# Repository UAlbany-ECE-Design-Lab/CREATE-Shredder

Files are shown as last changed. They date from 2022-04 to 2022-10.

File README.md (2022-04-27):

# CREATE-Shredder Extraction System 2021-2022 ReadMe

This ReadMe file uses Markdown formating.  Helpful cheat sheet is available here: 	[Markdown Cheat Sheet](https://www.markdownguide.org/cheat-sheet/)

## Team Members
Joseph Salgado - 
Michael George - 
Guillermo Esteban Mijancos
Team

## Hardware Dependencies
This project is very hardware oriented, and once we describe each item it will show how intuitive the hole system is.

1. We use a D/D Blower w/ Motor, 208-230/460 V. For our desired system we need a reliable and robust blower/motor
combination. This blower has an 11-inch turbine which is large enough to not get jammed or
clogged by small paper shreds. The motor that comes with this setup is a 1 horsepower 3
phase electric motor that can spin upwards of 3500 RPM. With our system, we plan on using
4 inches ducting for the inlet and the exhaust side and with a 4-inch outlet, this blower can
push nearly 560 CFM which should be plenty for our application
Motor

2. We use a 3 Phase 30A 3.7KW Maintained Self Lock On/Off Power Pushbutton Switch. It has ideal specifications to deal with the power needed by the motor and has the perfect 
functionality we are looking for our system. Once pressed On it maintains like that until we press the Off button.
Switch

3.We use a MODEL GN3442 GAYLORD COVER because the goal of the system designed in this project is to get the shredded paper
automatically into the big brown box provided by the mailing service company. In order to do
that, we require this component because the whole system works around a motor/blower
that creates wind gusts that would make kind of sloppy the whole movement of the paper.
This device provides a specific and convenient solution, covering the box and just letting the
tube with the shredded paper have access to it. This way, we use the cover until the box is
full and then easily remove it to get the shredded paper out.

gaylordCover

4.We use a 14/3 NM-B WG Romex Wire/Cable due to the fact that we are using a 3 phase motor/blower. This ware has three conductors and a neutral wire. The function of neutral wire in 3 phase 4 wire system is to serve as a return wire for general domestic supply system. The neutral is paired to each of the single phase load. The potential of the neutral point can be very well understood from the following Figure. The total neutral current is the vector sum of the three line currents. Under balanced conditions the vector sum is zero and therefore, the neutral current is zero

purpose-of-neutral-wire-in-three-pahse
Wiring

5.The plug in is adapted to the needs of the system and is a 20A, 3 pahse and 4 wiring black and white plug in with a capacity of 125/250V.

plugIn

6.We built a box, the inside has the shape of a rectangular frustum that works as a funnel for the paper to go through and avoid any possible clogging.
ShredderBin

7.To connect the box, the blower and the gaylord we used 4 inch semi-rigid galvanized steel pipes, that avoid clogging problems that you can find with materials like plastic.
Pipe

## Software Dependencies
To connect the different components of the system, we use 3D parts modeled by us in a customized way for the different needs of the project. We have used 3 parts. The first one connects the motor with the pipe that goes to the gaylord. The second one connects the box where the paper falls with the pipe that connects to the motor. The third one is on the other side of the tubing and connects to the motor.
BinDuct
BlowerExhaust
IntakeAdapter

## Steps Required to Replicate your Work. List the steps required to replicate your work
1. Wire the motor to be in low voltage mode by connecting T7 and T1 in line 1, T8 and T2 in line 2 and T9 and T3 in line 3.
2. Wire the different components together, the plug in with the switch, and the switch with the motor.
3. Set up the pipeline system between the motor and the two bins, the one under the shredder and the one that will leave the building.
## Concept
SystemOverview
## 3D Model
SystemOverall
## Resulting System
Mike

## Instruction Video: 

https://youtu.be/Mo4UCGreJuw

Winners

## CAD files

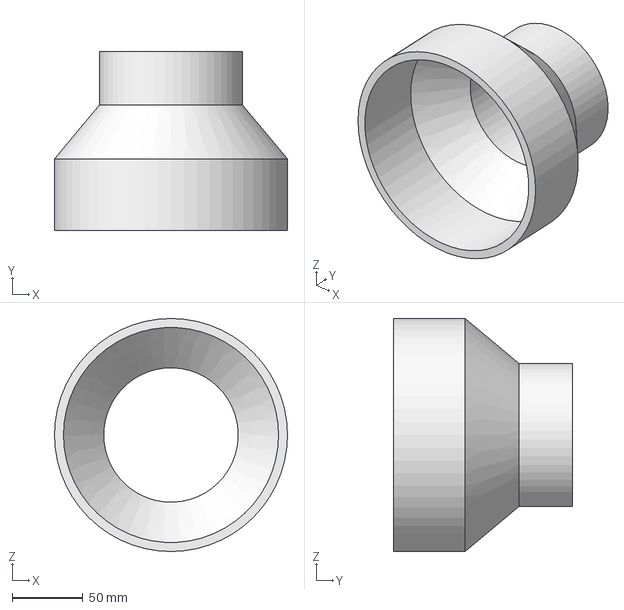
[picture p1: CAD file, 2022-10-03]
3D-Prints/IntakeAdapter0.25inLG..0.125inSM.RevA.FCStd
165.1 x 127.0 x 165.1 mm

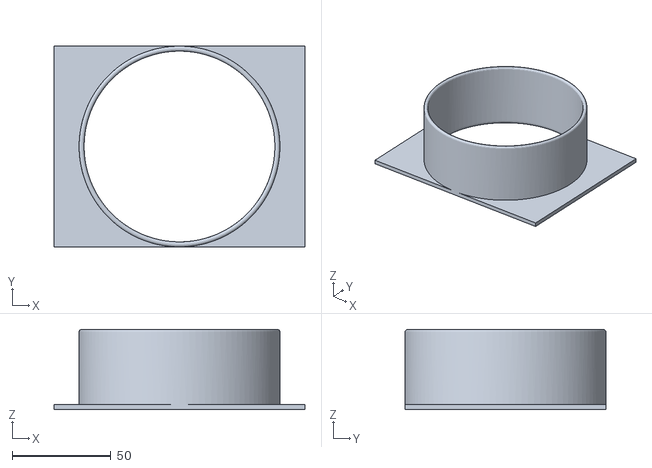
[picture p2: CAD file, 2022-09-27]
3D-Prints/Box Duct v7.stl
127.0 x 101.6 x 40.6

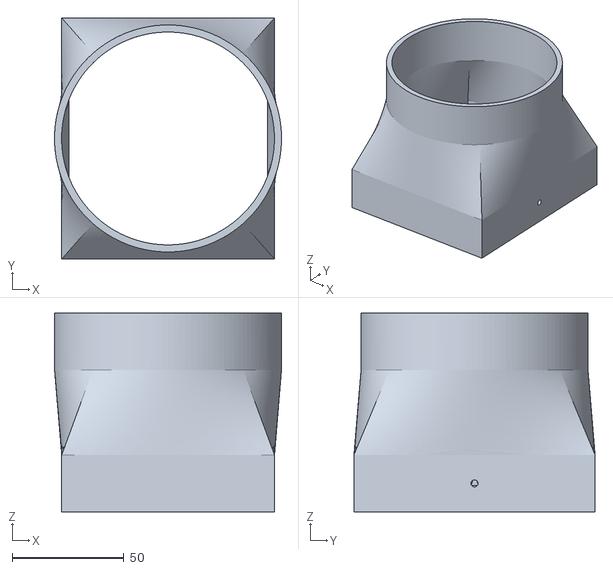
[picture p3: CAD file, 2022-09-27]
3D-Prints/Exhaust 2.stl
101.6 x 107.9 x 88.9

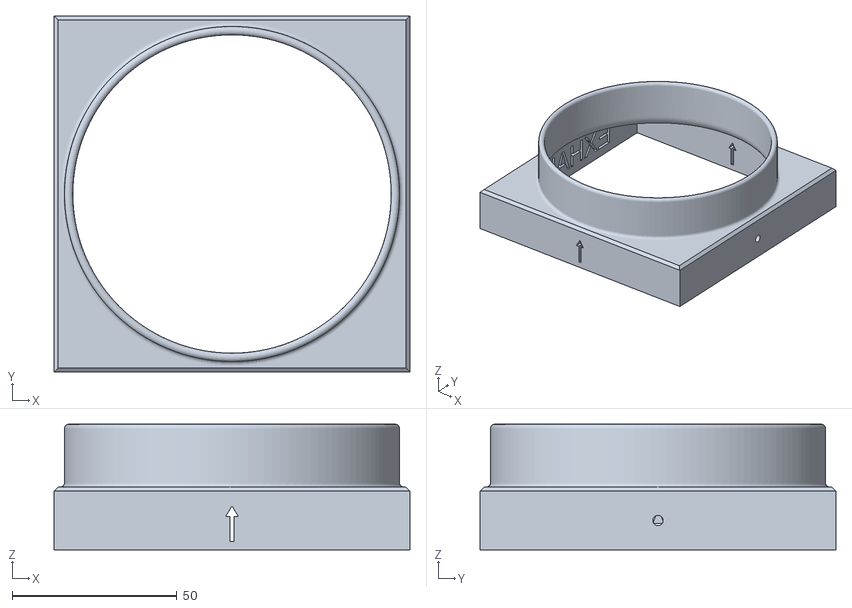
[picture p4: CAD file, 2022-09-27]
3D-Prints/Blower Exhaust v6.stl
107.9 x 107.9 x 38.1

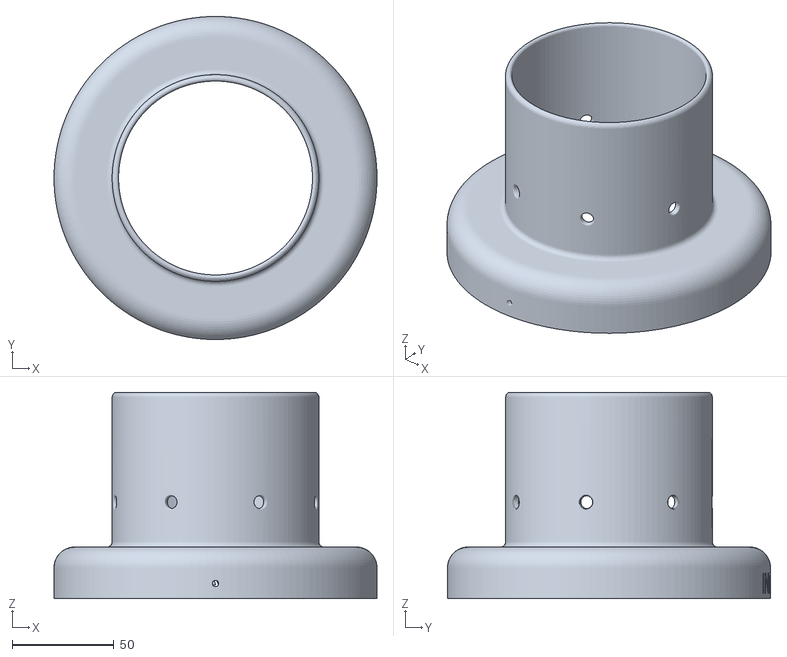
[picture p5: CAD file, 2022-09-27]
3D-Prints/Blower Intake v6.stl
158.7 x 158.7 x 101.4

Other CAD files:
3D-Prints/Intake 2.stl
3D-Prints/INTAKE 2 - No Holes v1.stl

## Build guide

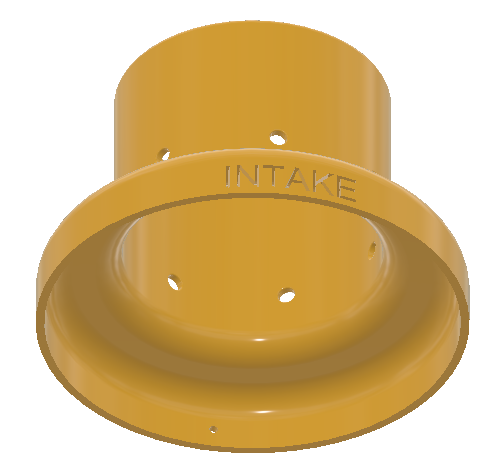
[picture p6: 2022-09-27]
3D-Prints/Screen Shot 2021-11-12 at 1.46.50 AM.png

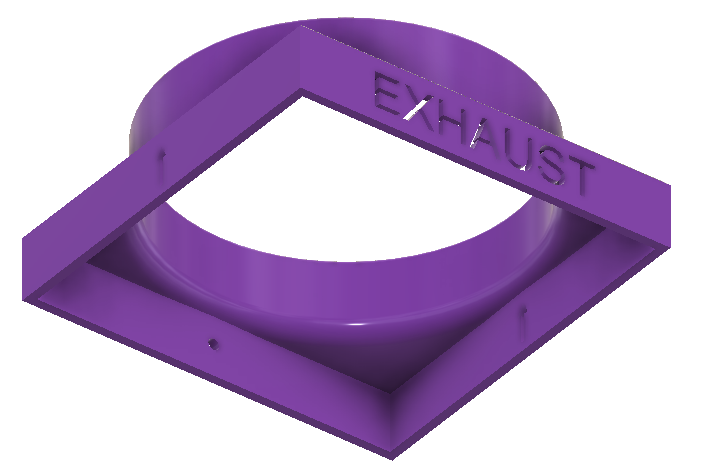
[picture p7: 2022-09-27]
3D-Prints/Screen Shot 2021-11-12 at 1.46.28 AM.png

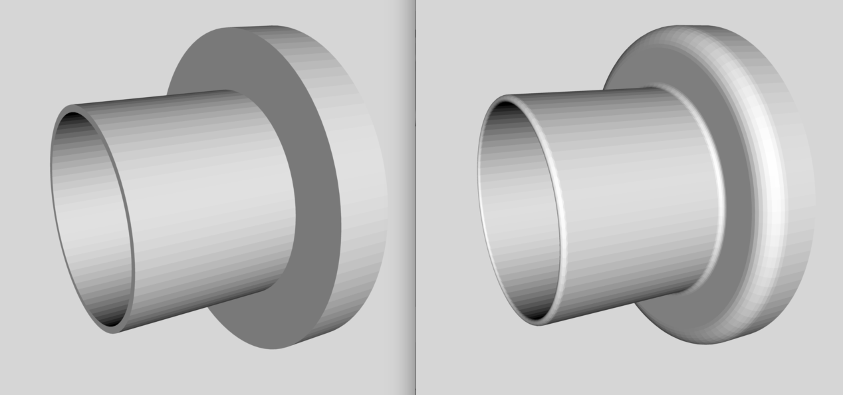
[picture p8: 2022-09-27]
3D-Prints/Screen Shot 2021-11-11 at 11.40.50 PM.png

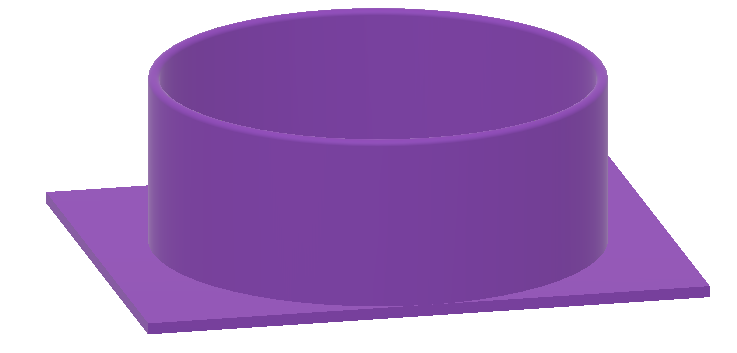
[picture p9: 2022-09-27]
3D-Prints/Screen Shot 2021-11-12 at 1.47.07 AM.png

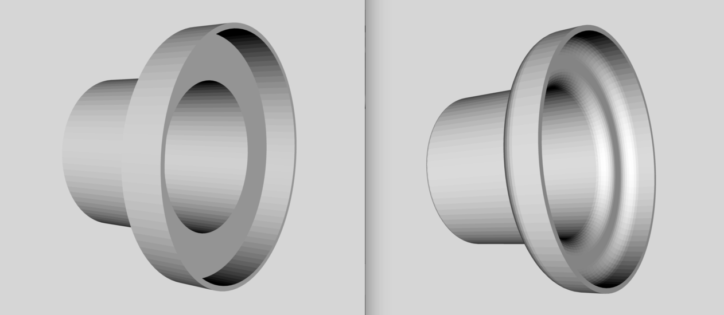
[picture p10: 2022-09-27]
3D-Prints/Screen Shot 2021-11-11 at 11.41.05 PM.png

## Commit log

2022-09-27 Included 3D printed STL files
    [Blower Exhaust v6.stl, Blower Intake v6.stl, Box Duct v7.stl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]
2022-10-03 CAD file for intake part
    [IntakeAdapter0.25inLG..0.125inSM.RevA.FCStd]
